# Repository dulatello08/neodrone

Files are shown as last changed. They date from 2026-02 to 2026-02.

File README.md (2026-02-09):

# NeoDrone v1

NeoDrone v1 is a compact all-in-one flight controller + 4-in-1 ESC board for small custom drones.

## Why I made this project

I wanted a cleaner drone stack with fewer separate boards, less wiring, and tighter integration between control and motor drive.  
This project is also a learning build to improve my PCB, embedded, and drone-systems workflow end to end.

## How to use this project

1. Clone this repository.
2. Pull firmware submodule:
   ```bash
   git submodule update --init --recursive
   ```
3. Open the hardware design in KiCad from `hardware/design/neodrone-v1.kicad_pro`.
4. Use firmware from `firmware/` (submodule) or project write-up links below.

Project links:

- [NeoDrone 3D model notes](https://dulatello08.me/blog/neodrone-3d-model/)
- [NeoDrone firmware notes](https://dulatello08.me/blog/neodrone-firmware/)
- [NeoDrone progress log #1](https://dulatello08.me/blog/neodrone-progress-1/)

### Full 3D model screenshot

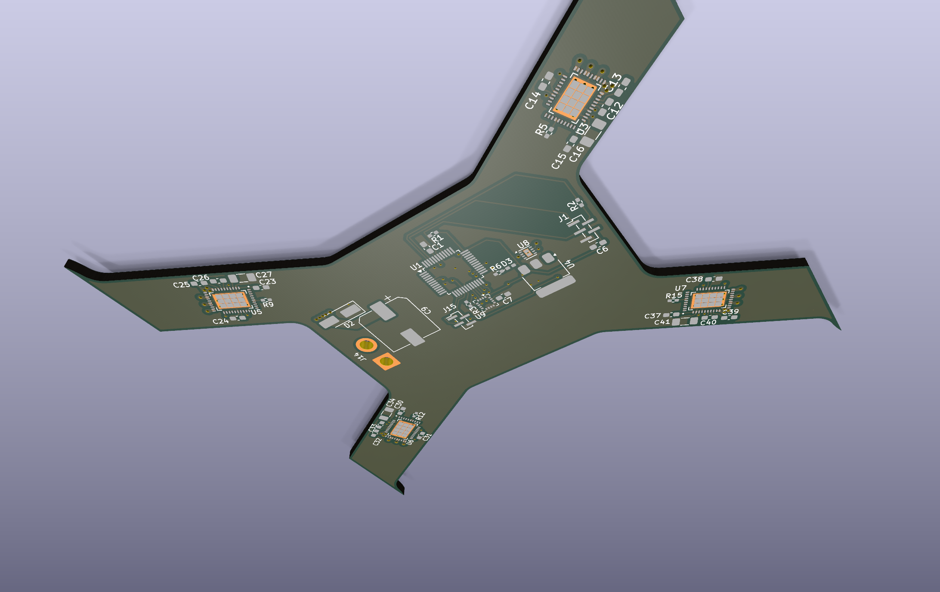
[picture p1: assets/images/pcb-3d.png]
NeoDrone v1 full 3D model


### PCB screenshot

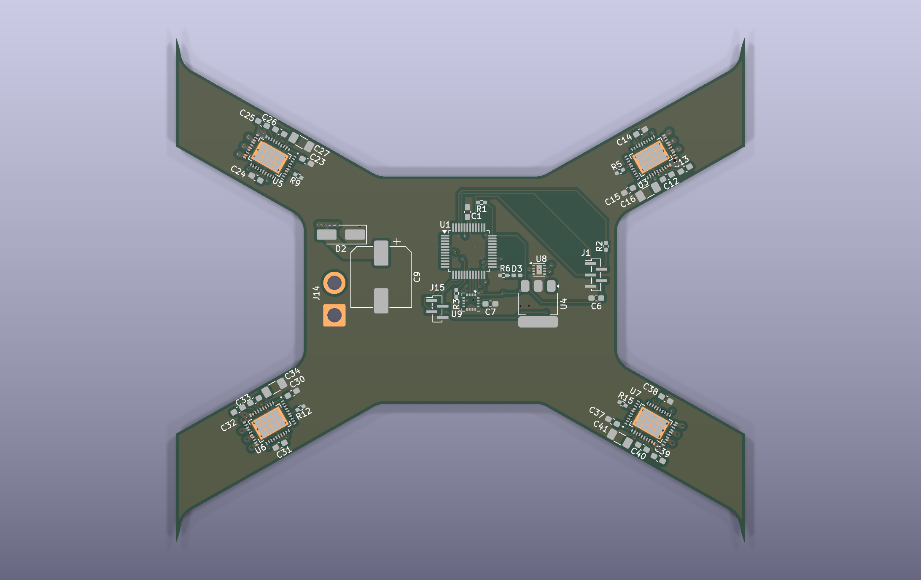
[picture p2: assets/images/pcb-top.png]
NeoDrone v1 PCB screenshot


### Wiring diagram

External wiring used: 4 motors (M1-M4), battery (VBAT/GND), and CRSF receiver (UART + power).

```mermaid
flowchart LR
  Battery["Battery"] --> FC["NeoDrone v1 Board"]
  FC --> M1["Motor 1"]
  FC --> M2["Motor 2"]
  FC --> M3["Motor 3"]
  FC --> M4["Motor 4"]
  CRSF["CRSF Receiver"] --> FC
```

## BOM (truncated)

Full BOM export is in `bom.csv`.  
This is a shortened reference table with links:

| Reference | Part | MPN | Qty | Link |
|---|---|---|---:|---|
| U1 | Main MCU | ATSAMD21G18A-AU | 1 | [Digi-Key](https://www.digikey.com/en/products/result?keywords=ATSAMD21G18A-AU-ND) |
| U3, U5, U6, U7 | 3-phase motor driver | MCF8316A1VRGFR | 4 | [Digi-Key](https://www.digikey.com/en/products/result?keywords=296-MCF8316A1VRGFRCT-ND) |
| U4 | 3.3V regulator | MCP1826S-3302E/DB | 1 | [Digi-Key](https://www.digikey.com/en/products/result?keywords=MCP1826S-3302E%2FDB-ND) |
| U8 | 5V buck regulator | TPS62163DSGT | 1 | [Digi-Key](https://www.digikey.com/en/products/result?keywords=296-30228-1-ND) |
| U9 | IMU | ICM-20602 | 1 | [Digi-Key](https://www.digikey.com/en/products/result?keywords=1428-1060-1-ND) |
| Q1 | P-channel MOSFET | SI7139DP-T1-GE3 | 1 | [Digi-Key](https://www.digikey.com/en/products/result?keywords=SI7139DP-T1-GE3CT-ND) |
| L1-L5 | 2.2uH inductors | SRN2510BTA-2R2M | 5 | [Digi-Key](https://www.digikey.com/en/products/result?keywords=118-SRN2510BTA-2R2MCT-ND) |
| D1 | 12V zener diode | BZT52B12 RHG | 1 | [Digi-Key](https://www.digikey.com/en/products/result?keywords=BZT52B12RHGCT-ND) |
| D2 | TVS diode | SMAJ18A-13-F | 1 | [Digi-Key](https://www.digikey.com/en/products/result?keywords=SMAJ18A-FDICT-ND) |
| C9 | Bulk electrolytic cap | EEE-FP1E331AP | 1 | [Digi-Key](https://www.digikey.com/en/products/result?keywords=PCE4439CT-ND) |

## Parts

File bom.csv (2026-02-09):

Index | Manufacturer Part Number | Manufacturer Name | Description | Lead Time | Availability | Stock Status | Attrition % | Requested Quantity 1 | Pack Quantity 1 | Pack Type 1 | Digi-Key Part Number 1 | Unit Price 1 | Extended Price 1 | Minimum Order Quantity 1 | Customer Reference | Requested Part Number | Lead Weeks | Datasheet | Reference Designator | US Import Tariff | Note | Part Status | RoHS Status | REACH Status | Moisture Sensitivity Level (MSL) | ECCN | HTSUS | Country of Origin | Environmental Information | Original Part numbers | Unit of Measure | Image | Product Notes
1 | GCM188R71C105KA64D | Murata Electronics | CAP CER 1UF 16V X7R 0603 |  | 600,773 | In Stock | 10 | 13 | 15 | Cut Tape (CT) | 490-5241-1-ND | 0.08500 | $1.28 | 1 |  | 490-5241-1-ND | 16 | https://pim.murata.com/asset/pim4/ceramicCapacitorSMD/GCM188R71C105KA64-04A-EN_PDF_CERAMICCAPACITORSMD |  | - |  | Active | ROHS3 Compliant | REACH Unaffected | 1 (Unlimited) | EAR99 | 8532.24.0020 | Philippines |  | 490-5241-1-ND | EACH | https://mm.digikey.com/Volume0/opasdata/d220001/medias/images/4850/490_0603%20%281608%20metric%29.jpg
2 | CC1206KKX5R8BB226 | YAGEO | CAP CER 22UF 25V X5R 1206 |  | 1,675 | In Stock | 10 | 10 | 11 | Cut Tape (CT) | 13-CC1206KKX5R8BB226CT-ND | 0.38600 | $4.25 | 1 |  | 13-CC1206KKX5R8BB226CT-ND | 24 | https://yageogroup.com/content/datasheet/asset/file/UPY-GPHC_X5R_4V-TO-50V |  | - |  | Active | ROHS3 Compliant | REACH Unaffected | 1 (Unlimited) | EAR99 | 8532.24.0020 | Taiwan |  | 1276-3047-1-ND | EACH | https://mm.digikey.com/Volume0/opasdata/d220001/medias/images/4848/13_1206-%283216-Metric%29-1%2C45mm.jpg
3 | GRM188R72A104KA35D | Murata Electronics | CAP CER 0.1UF 100V X7R 0603 |  | 1,699,041 | In Stock | 10 | 12 | 14 | Cut Tape (CT) | 490-3285-1-ND | 0.08700 | $1.22 | 1 |  | 490-3285-1-ND | 12 | https://search.murata.co.jp/Ceramy/image/img/A01X/G101/ENG/GRM188R72A104KA35-01.pdf |  | - |  | Active | ROHS3 Compliant | REACH Unaffected | 1 (Unlimited) | EAR99 | 8532.24.0020 | Japan |  | 490-3285-1-ND | EACH | https://mm.digikey.com/Volume0/opasdata/d220001/medias/images/4322/cut-tape-render.jpg
4 | CGJ3E2X7R1H473K080AA | TDK Corporation | CAP CER 0.047UF 50V X7R 0603 |  | 9,349 | In Stock - Non-Stock | 10 | 4 | 5 | Cut Tape (CT) | 445-8120-1-ND | 0.17000 | $0.85 | 1 |  | 445-8120-1-ND | 36 | https://product.tdk.com/en/system/files/dam/doc/product/capacitor/ceramic/mlcc/catalog/mlcc_highreliability_general_en.pdf |  | - |  | Obsolete | ROHS3 Compliant | REACH Unaffected | 1 (Unlimited) | EAR99 | 8532.24.0020 | Japan | https://product.tdk.com/system/files/dam/doc/product/capacitor/ceramic/mlcc/rohs/mlccrohs_highreliability_general_en.pdf|https://product.tdk.com/en/environment/index.html | 445-8120-1-ND | EACH | https://mm.digikey.com/Volume0/opasdata/d220001/medias/images/2640/MFG_CGJ3E2X7R1H473K080AA.jpg
5 | CL10A106MA8NRNC | Samsung Electro-Mechanics | CAP CER 10UF 25V X5R 0603 |  | 655,915 | In Stock | 10 | 3 | 4 | Cut Tape (CT) | 1276-1869-1-ND | 0.09000 | $0.36 | 1 |  | 1276-1869-1-ND | 31 | https://mm.digikey.com/Volume0/opasdata/d220001/medias/docus/658/CL10A106MA8NRNC_Spec.pdf |  | - |  | Active | ROHS3 Compliant | REACH Unaffected | 1 (Unlimited) | EAR99 | 8532.24.0020 | China | https://www.samsungsem.com/files/fileDown.do?key=ed1dfdfa-645e-4252-b707-17f9b1502dd1|https://www.samsungsem.com/global/support/certificate/product-stewardship.do | 1276-1869-1-ND | EACH | https://mm.digikey.com/Volume0/opasdata/d220001/medias/images/2537/Ceramic-Capacitor-CL-Series.jpg
6 | CC0402KRX7R9BB103 | YAGEO | CAP CER 10000PF 50V X7R 0402 |  | 2,772,907 | In Stock | 10 | 1 | 2 | Cut Tape (CT) | 311-1349-1-ND | 0.08000 | $0.16 | 1 |  | 311-1349-1-ND | 16 | https://yageogroup.com/content/datasheet/asset/file/UPY-GPHC_X7R_6_3V-TO-250V |  | - |  | Active | ROHS3 Compliant | REACH Unaffected | 1 (Unlimited) | EAR99 | 8532.24.0020 | Taiwan |  | 311-1349-1-ND | EACH | https://mm.digikey.com/Volume0/opasdata/d220001/medias/images/4322/cut-tape-render.jpg
7 | GRM188R61H225KE11D | Murata Electronics | CAP CER 2.2UF 50V X5R 0603 |  | 74,531 | In Stock | 10 | 1 | 2 | Cut Tape (CT) | 490-10733-1-ND | 0.25000 | $0.50 | 1 |  | 490-10733-1-ND | 12 | https://search.murata.co.jp/Ceramy/image/img/A01X/G101/ENG/GRM188R61H225KE11-01.pdf |  | - |  | Active | ROHS3 Compliant | REACH Unaffected | 1 (Unlimited) | EAR99 | 8532.24.0020 | Japan |  | 490-10733-1-ND | EACH | https://mm.digikey.com/Volume0/opasdata/d220001/medias/images/4322/cut-tape-render.jpg
8 | GRM188R61E475KE11D | Murata Electronics | CAP CER 4.7UF 25V X5R 0603 |  | 286,809 | In Stock | 10 | 1 | 2 | Cut Tape (CT) | 490-7203-1-ND | 0.08000 | $0.16 | 1 |  | 490-7203-1-ND | 12 | https://search.murata.co.jp/Ceramy/image/img/A01X/G101/ENG/GRM188R61E475KE11-01.pdf |  | - |  | Active | ROHS3 Compliant | REACH Unaffected | 1 (Unlimited) | EAR99 | 8532.24.0020 | Japan |  | 490-7203-1-ND | EACH | https://mm.digikey.com/Volume0/opasdata/d220001/medias/images/4322/cut-tape-render.jpg
9 | EEE-FP1E331AP | Panasonic Electronic Components | CAP ALUM 330UF 20% 25V SMD |  | 14,767 | In Stock | 10 | 1 | 2 | Cut Tape (CT) | PCE4439CT-ND | 1.00000 | $2.00 | 1 |  | PCE4439CT-ND | 18 | https://industrial.panasonic.com/ww/products/pt/aluminum-cap-smd/models/EEEFP1E331AP |  | - |  | Active | ROHS3 Compliant | REACH Unaffected | 1 (Unlimited) | EAR99 | 8532.22.0020 | Malaysia |  | PCE4439CT-ND | EACH | https://mm.digikey.com/Volume0/opasdata/d220001/medias/images/634/EEE-FP1V221AP.JPG
10 | BZT52B12 RHG | Taiwan Semiconductor Corporation | DIODE ZENER 12V 500MW SOD123F |  | 7,787 | In Stock | 10 | 1 | 2 | Cut Tape (CT) | BZT52B12RHGCT-ND | 0.15000 | $0.30 | 1 |  | BZT52B12RHGCT-ND | 18 | https://services.taiwansemi.com/storage/resources/datasheet/BZT52B2V4 series_F15.pdf |  | - |  | Active | ROHS3 Compliant | REACH Unaffected | 1 (Unlimited) | EAR99 | 8541.10.0050 | Taiwan | https://www.taiwansemi.com/en/wp-content/uploads/2023/12/Environment_Hazardous_Substances_Compliance_20231115.pdf|https://www.taiwansemi.com/en/wp-content/uploads/2023/12/REACH_regulation1907_2006_EC_compliance_240%20SVHCs_20240124_Web.pdf|https://services.taiwansemi.com/storage/resources/environmental_information/REACH%20regulation%20compliance_ANNEX%20XVII_20250708_Web.pdf|https://www.taiwansemi.com/en/wp-content/uploads/2023/12/California%20Proposition%2065%20Compliance_20240124_Web.pdf | 1727-1597-1-ND | EACH | https://mm.digikey.com/Volume0/opasdata/d220001/medias/images/6241/1801%7ESOD123F%7E%7E2_view2.jpg
11 | SMAJ18A-13-F | Diodes Incorporated | TVS DIODE 18VWM 29.2VC SMA |  | 113,230 | In Stock | 10 | 1 | 2 | Cut Tape (CT) | SMAJ18A-FDICT-ND | 0.20000 | $0.40 | 1 |  | SMAJ18A-FDICT-ND | 12 | https://www.diodes.com/assets/Datasheets/SMAJ5.0CA-SMAJ200CA.pdf |  | - |  | Active | ROHS3 Compliant | REACH Unaffected | 1 (Unlimited) | EAR99 | 8541.10.0080 | Taiwan | https://mm.digikey.com/Volume0/opasdata/d220001/medias/docus/6731/Diode%20RoHS3%20REACH%20247%20Jan%202025%20Statement.pdf | 1655-SMAJ18ACT-ND | EACH | https://mm.digikey.com/Volume0/opasdata/d220001/medias/images/5787/31%7ESMA%7E%7E2-View-2.jpg
12 | LTST-C281KRKT | Lite-On Inc. | LED RED CLEAR CHIP SMD |  | 21,252 | In Stock | 10 | 1 | 2 | Cut Tape (CT) | 160-LTST-C281KRKTCT-ND | 0.18000 | $0.36 | 1 |  | 160-LTST-C281KRKTCT-ND | 22 | https://optoelectronics.liteon.com/upload/download/DS22-2008-0117/LTST-C281KRKT.pdf |  | May apply on shipments to the U.S. |  | Active | ROHS3 Compliant | REACH Unaffected | 2A (4 Weeks) | EAR99 | 8541.41.0000 | China |  | 160-LTST-C281KRKTCT-ND | EACH | https://mm.digikey.com/Volume0/opasdata/d220001/derivates/6/003/237/303/%7E160%7E0402-%281005-Metric%29%7E.002_web%28640x640%29.jpg
13 | BC070-05-A-1-L-C | GCT | 5POS 1.0MM PITCH SOCKET, SIL, SM |  | 2,899 | In Stock |  | 1 | 1 | Cut Tape (CT) | 2073-BC070-05-A-1-L-CCT-ND | 1.03000 | $1.03 | 1 |  | 2073-BC070-05-A-1-L-CCT-ND | 8 | https://gct.co/files/specs/1.00mm-socket-spec.pdf |  | May apply on shipments to the U.S. |  | Active | ROHS3 Compliant | REACH Unaffected | 1 (Unlimited) | EAR99 | 8536.69.4040 | China | https://gct.co/files/info/gct_certificate_of_compliance.pdf | 2073-BC070-05-A-1-L-CCT-ND | EACH | https://mm.digikey.com/Volume0/opasdata/d220001/medias/images/438/MFG_BC070-05-A-1-L-C.jpg
14 | BC070-04-A-1-L-D | GCT | 4W, 1.0MM PITCH SOCKET, SIL, SMT |  | 2,866 | In Stock |  | 1 | 1 | Tube | 2073-BC070-04-A-1-L-D-ND | 0.52000 | $0.52 | 1 |  | 2073-BC070-04-A-1-L-D-ND | 8 | https://gct.co/files/specs/1.00mm-socket-spec.pdf |  | May apply on shipments to the U.S. |  | Active | ROHS3 Compliant | REACH Unaffected | 1 (Unlimited) | EAR99 | 8536.69.4040 | China | https://gct.co/files/info/gct_certificate_of_compliance.pdf | 2073-BC070-04-A-1-L-D-ND | EACH | https://mm.digikey.com/Volume0/opasdata/d220001/medias/images/4059/BC070-04-A-1-L-D.jpg
15 | SRN2510BTA-2R2M | Bourns Inc. | FIXED IND 2.2UH 2A 132 MOHM SMD |  | 2,140 | In Stock | 10 | 5 | 6 | Cut Tape (CT) | 118-SRN2510BTA-2R2MCT-ND | 0.30000 | $1.80 | 1 |  | 118-SRN2510BTA-2R2MCT-ND | 21 | https://www.bourns.com/docs/Product-Datasheets/SRN2510BTA.pdf |  | May apply on shipments to the U.S. |  | Active | ROHS3 Compliant | REACH Unaffected | 1 (Unlimited) | EAR99 | 8504.50.8000 | China | https://mm.digikey.com/Volume0/opasdata/d220001/medias/docus/6657/Bourns%20REACH%20247%20Jan%202025%20Statement.pdf|https://www.bourns.com/docs/rohs-cofc/cofc-srn.pdf?sfvrsn=597d93f1_18 | 118-SRN2510BTA-2R2MCT-ND | EACH | https://mm.digikey.com/Volume0/opasdata/d220001/derivates/6/001/152/398/MFG_SRN2510BTA_web%28640x640%29.jpg
16 | SI7139DP-T1-GE3 | Vishay Siliconix | MOSFET P-CH 30V 40A PPAK SO-8 |  | 4,126 | In Stock |  | 1 | 1 | Cut Tape (CT) | SI7139DP-T1-GE3CT-ND | 2.09000 | $2.09 | 1 |  | SI7139DP-T1-GE3CT-ND | 39 | https://www.vishay.com/docs/65299/si7139dp.pdf |  | May apply on shipments to the U.S. |  | Active | ROHS3 Compliant |  | 1 (Unlimited) | EAR99 | 8541.29.0095 | China |  | SI7139DP-T1-GE3CT-ND | EACH | https://mm.digikey.com/Volume0/opasdata/d220001/derivates/6/003/212/993/742%7E5881%7EDP%7E8_web%28640x640%29.jpg
17 | RC0402FR-0710KL | YAGEO | RES 10K OHM 1% 1/16W 0402 |  | 9,636,776 | In Stock | 10 | 10 | 11 | Cut Tape (CT) | 311-10.0KLRCT-ND | 0.01200 | $0.13 | 1 |  | 311-10.0KLRCT-ND | 18 | https://yageogroup.com/content/datasheet/asset/file/PYU-RC_GROUP_51_ROHS_L |  | - |  | Active | ROHS3 Compliant | REACH Unaffected | 1 (Unlimited) | EAR99 | 8533.21.0030 | Taiwan | https://www.yageogroup.com/content/Resource%20Library/Product%20Environmental%20Compliance/RoHS_Compliance_YAGEO.pdf | 311-10.0KLRCT-ND | EACH | https://mm.digikey.com/Volume0/opasdata/d220001/medias/images/4322/cut-tape-render.jpg
18 | RC0402FR-07100KL | YAGEO | RES 100K OHM 1% 1/16W 0402 |  | 4,831,519 | In Stock | 10 | 1 | 2 | Cut Tape (CT) | 311-100KLRCT-ND | 0.10000 | $0.20 | 1 |  | 311-100KLRCT-ND | 18 | https://yageogroup.com/content/datasheet/asset/file/PYU-RC_GROUP_51_ROHS_L |  | - |  | Active | ROHS3 Compliant | REACH Unaffected | 1 (Unlimited) | EAR99 | 8533.21.0030 | Taiwan | https://www.yageogroup.com/content/Resource%20Library/Product%20Environmental%20Compliance/RoHS_Compliance_YAGEO.pdf | 311-100KLRCT-ND | EACH | https://mm.digikey.com/Volume0/opasdata/d220001/medias/images/4322/cut-tape-render.jpg
19 | RC0402FR-0733RL | YAGEO | RES 33 OHM 1% 1/16W 0402 |  | 2,592,460 | In Stock | 10 | 1 | 2 | Cut Tape (CT) | 311-33.0LRCT-ND | 0.10000 | $0.20 | 1 |  | 311-33.0LRCT-ND | 18 | https://yageogroup.com/content/datasheet/asset/file/PYU-RC_GROUP_51_ROHS_L |  | - |  | Active | ROHS3 Compliant | REACH Unaffected | 1 (Unlimited) | EAR99 | 8533.21.0030 | Taiwan | https://www.yageogroup.com/content/Resource%20Library/Product%20Environmental%20Compliance/RoHS_Compliance_YAGEO.pdf | 311-33.0LRCT-ND | EACH | https://mm.digikey.com/Volume0/opasdata/d220001/medias/images/4322/cut-tape-render.jpg
20 | RC0402FR-07220RL | YAGEO | RES 220 OHM 1% 1/16W 0402 |  | 410,791 | In Stock | 10 | 1 | 2 | Cut Tape (CT) | 311-220LRCT-ND | 0.10000 | $0.20 | 1 |  | 311-220LRCT-ND | 18 | https://yageogroup.com/content/datasheet/asset/file/PYU-RC_GROUP_51_ROHS_L |  | - |  | Active | ROHS3 Compliant | REACH Unaffected | 1 (Unlimited) | EAR99 | 8533.21.0030 | Taiwan | https://www.yageogroup.com/content/Resource%20Library/Product%20Environmental%20Compliance/RoHS_Compliance_YAGEO.pdf | 311-220LRCT-ND | EACH | https://mm.digikey.com/Volume0/opasdata/d220001/medias/images/4322/cut-tape-render.jpg
21 | ATSAMD21G18A-AU | Microchip Technology | IC MCU 32BIT 256KB FLASH 48TQFP |  | 6,577 | In Stock |  | 1 | 1 | Tray | ATSAMD21G18A-AU-ND | 4.16000 | $4.16 | 1 |  | ATSAMD21G18A-AU-ND | 4 | https://ww1.microchip.com/downloads/en/DeviceDoc/SAM-D21-DA1-Family-Data-Sheet-DS40001882H.pdf |  | - |  | Active | ROHS3 Compliant | REACH Unaffected | 3 (168 Hours) | 3A991A2 | 8542.31.0025 | Thailand | https://ww1.microchip.com/downloads/aemDocuments/documents/corporate-responsibilty/environmental/product-regulatory-information/Semiconductor_EnvCoC.pdf|https://ww1.microchip.com/downloads/aemDocuments/documents/corporate-responsibilty/environmental/product-regulatory-information/Microchip_REACH_Statement.pdf | ATSAMD21G18A-AU-ND | EACH | https://mm.digikey.com/Volume0/opasdata/d220001/medias/images/4578/150%7E48TQFP-1%2C2-7x7%7EA%7E48.JPG
22 | MCF8316A1VRGFR | Texas Instruments | 40-V MAX, 8-A PEAK, SENSORLESS F |  | 3,958 | In Stock |  | 4 | 4 | Cut Tape (CT) | 296-MCF8316A1VRGFRCT-ND | 3.91000 | $15.64 | 1 |  | 296-MCF8316A1VRGFRCT-ND | 12 | https://www.ti.com/lit/ds/symlink/mcf8316a.pdf?ts=1662971630101 |  | - |  | Active | Not applicable |  | 2 (1 Year) | EAR99 | 8542.39.0070 | China |  | 296-MCF8316A1VRGFRCT-ND | EACH | https://mm.digikey.com/Volume0/opasdata/d220001/derivates/6/003/210/417/296%7E4204716-3%7ERGF%7E40_web%28640x640%29.jpg
23 | MCP1826S-3302E/DB | Microchip Technology | IC REG LINEAR 3.3V 1A SOT-223-3 |  | 9,244 | In Stock |  | 1 | 1 | Tube | MCP1826S-3302E/DB-ND | 0.91000 | $0.91 | 1 |  | MCP1826S-3302E/DB-ND | 4 | https://ww1.microchip.com/downloads/en/DeviceDoc/22057B.pdf |  | - |  | Active | ROHS3 Compliant | REACH Unaffected | 1 (Unlimited) | EAR99 | 8542.39.0090 | Thailand | https://ww1.microchip.com/downloads/aemDocuments/documents/corporate-responsibilty/environmental/product-regulatory-information/Semiconductor_EnvCoC.pdf|https://ww1.microchip.com/downloads/aemDocuments/documents/corporate-responsibilty/environmental/product-regulatory-information/Microchip_REACH_Statement.pdf | MCP1826S-3302E/DB-ND | EACH | https://mm.digikey.com/Volume0/opasdata/d220001/medias/images/5484/150%7EC04-032%7EDB%7E4.JPG
24 | TPS62163DSGT | Texas Instruments | IC REG BUCK 5V 1A 8WSON |  | 8,333 | In Stock |  | 1 | 1 | Cut Tape (CT) | 296-30228-1-ND | 1.98000 | $1.98 | 1 |  | 296-30228-1-ND | 12 | https://www.ti.com/general/docs/suppproductinfo.tsp?distId=10 |  | - |  | Active | ROHS3 Compliant | REACH Unaffected | 2 (1 Year) | EAR99 | 8542.39.0090 | Malaysia |  | 296-30228-1-ND | EACH | https://mm.digikey.com/Volume0/opasdata/d220001/medias/images/339/296%7E4208210%7EDSG%7E8.jpg
25 | ICM-20602 | TDK InvenSense | IMU ACCEL/GYRO/TEMP I2C/SPI LGA |  | 75 | In Stock |  | 1 | 1 | Cut Tape (CT) | 1428-1060-1-ND | 4.96000 | $4.96 | 1 |  | 1428-1060-1-ND | 26 | https://www.invensense.com/wp-content/uploads/2016/10/DS-000176-ICM-20602-v1.0.pdf |  | - |  | Last Time Buy | ROHS3 Compliant | REACH Unaffected | 3 (168 Hours) | 7A994 | 8542.39.0070 | Taiwan |  | 1428-1060-1-ND | EACH | https://mm.digikey.com/Volume0/opasdata/d220001/medias/images/6154/1428%7E16LGA-.80-3X3%7E%7E16.jpg

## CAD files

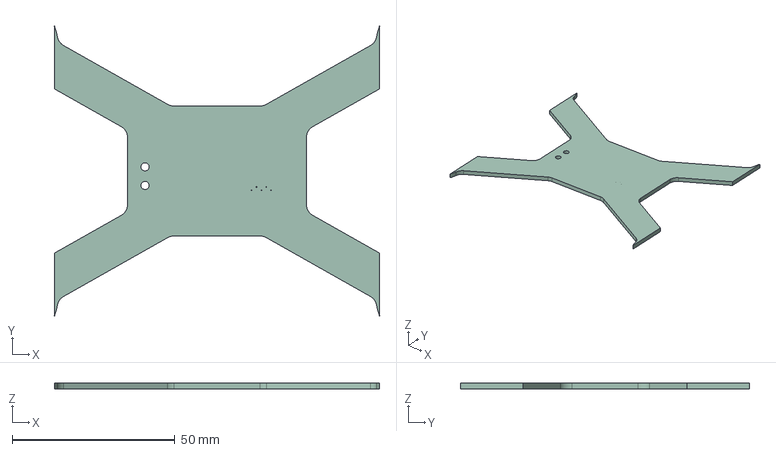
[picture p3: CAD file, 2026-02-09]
hardware/3d/neodrone-v1.step
100.0 x 89.0 x 1.84 mm

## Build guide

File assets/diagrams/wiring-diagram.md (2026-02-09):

# NeoDrone v1 wiring diagram

Current planned wiring:

- 4 motors connected directly to board outputs M1-M4
- battery connected to VBAT and GND
- CRSF receiver connected to power and UART (TX/RX + GND)

```mermaid
flowchart LR
  Battery["Battery"] --> FC["NeoDrone v1 Board"]
  FC --> M1["Motor 1"]
  FC --> M2["Motor 2"]
  FC --> M3["Motor 3"]
  FC --> M4["Motor 4"]
  CRSF["CRSF Receiver"] --> FC
```

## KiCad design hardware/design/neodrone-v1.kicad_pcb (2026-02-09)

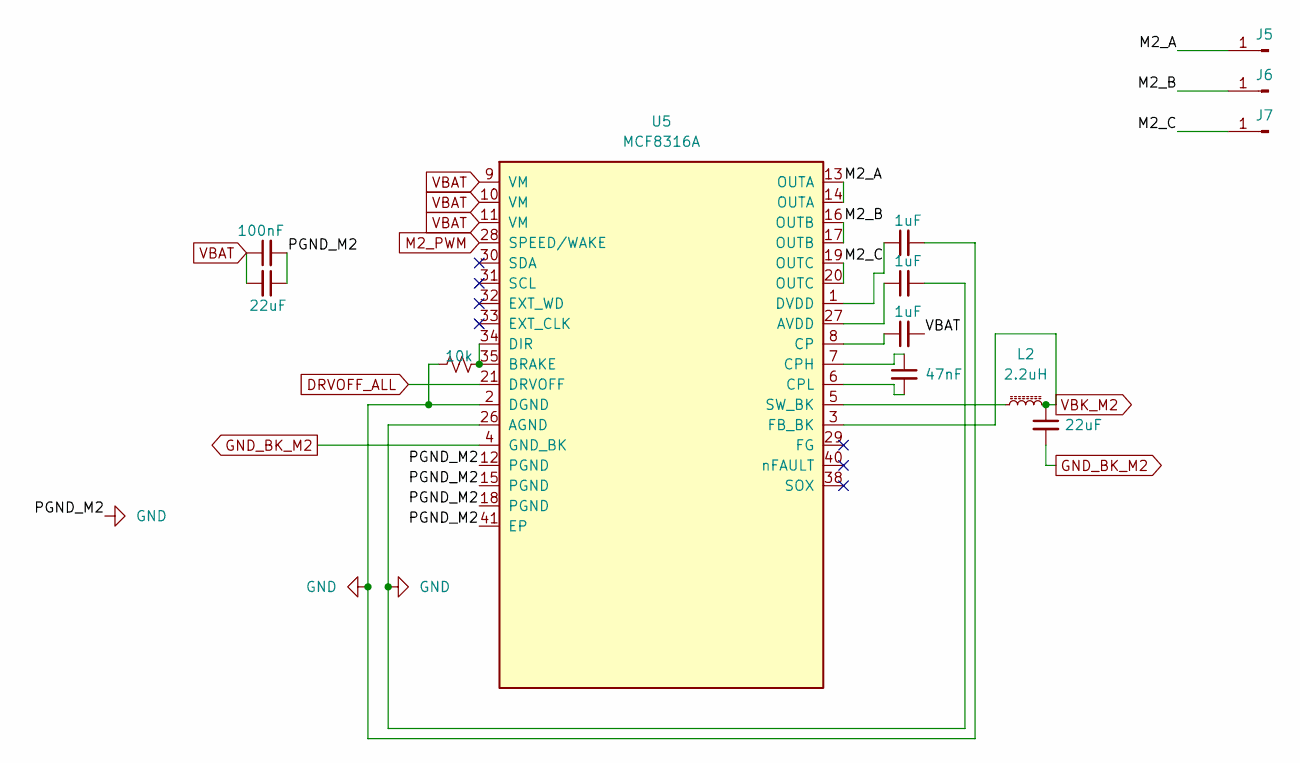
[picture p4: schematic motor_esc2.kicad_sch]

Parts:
C21: 100nF; C_0603_1608Metric_Pad1.08x0.95mm_HandSolder
C22, C27: 22uF; C_1206_3216Metric_Pad1.33x1.80mm_HandSolder
C23, C24, C25: 1uF; C_0603_1608Metric_Pad1.08x0.95mm_HandSolder
C26: 47nF; C_0603_1608Metric_Pad1.08x0.95mm_HandSolder
J5, J6, J7: SolderWirePad_1x01_SMD_2x4mm
L2: 2.2uH; L_1008_2520Metric_Pad1.43x2.20mm_HandSolder
R9: 10k; R_0402_1005Metric_Pad0.72x0.64mm_HandSolder
U5: MCF8316A; MCF8316A_RGF0040E_VQFN-40-1EP_7x5mm_P0.5mm_EP5.5x3.5mm

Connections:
/motor_esc2/M2_A: J5.1, U5.13 (OUTA), U5.14 (OUTA)
/motor_esc2/M2_B: J6.1, U5.16 (OUTB), U5.17 (OUTB)
/motor_esc2/M2_C: J7.1, U5.19 (OUTC), U5.20 (OUTC)
DRVOFF_ALL: U5.21 (DRVOFF); also elsewhere on the board
GND: C21.2, C22.1, C23.2, C24.2, C27.2, R9.1, U5.2 (DGND), U5.4 (GND_BK), U5.12 (PGND), U5.15 (PGND), U5.18 (PGND), U5.26 (AGND), U5.41 (EP); also elsewhere on the board
M2_PWM: U5.28 (SPEED/WAKE); also elsewhere on the board
unnamed: C24.1, U5.27 (AVDD)
unnamed: R9.2, U5.34 (DIR), U5.35 (BRAKE)
unnamed: C25.1, U5.8 (CP)
unnamed: C26.1, U5.7 (CPH)
unnamed: C26.2, U5.6 (CPL)
unnamed: C23.1, U5.1 (DVDD)
unnamed: L2.1, U5.5 (SW_BK)
VBAT: C21.1, C22.2, C25.2, U5.9 (VM), U5.10 (VM), U5.11 (VM); also elsewhere on the board
VBK_M2: C27.1, L2.2, U5.3 (FB_BK)

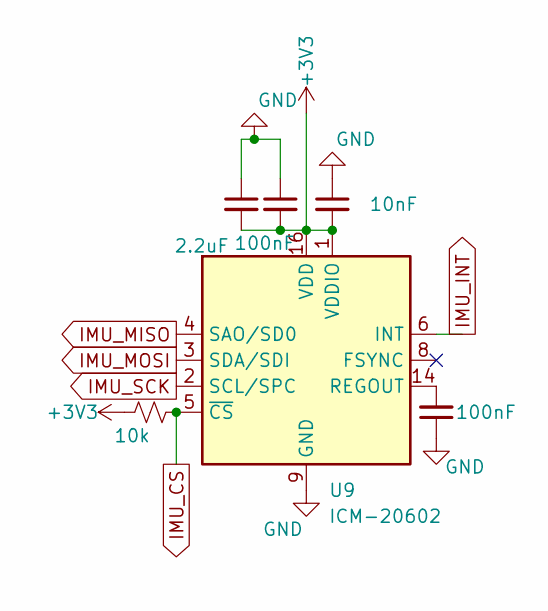
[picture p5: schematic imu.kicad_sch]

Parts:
C7, C8: 100nF; C_0603_1608Metric_Pad1.08x0.95mm_HandSolder
C44: 10nF; C_0402_1005Metric_Pad0.74x0.62mm_HandSolder
C45: 2.2uF; C_0603_1608Metric_Pad1.08x0.95mm_HandSolder
R3: 10k; R_0402_1005Metric_Pad0.72x0.64mm_HandSolder
U9: ICM-20602; LGA-16_3x3mm_P0.5mm

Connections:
+3V3: C8.2, C44.2, C45.2, R3.1, U9.1 (VDDIO), U9.16 (VDD); also elsewhere on the board
GND: C7.1, C8.1, C44.1, C45.1, U9.9 (GND), U9.10 (GND), U9.11 (GND), U9.12 (GND), U9.13 (GND), U9.15 (GND); also elsewhere on the board
IMU_CS: R3.2, U9.5 (~CS); also elsewhere on the board
IMU_INT: U9.6 (INT); also elsewhere on the board
IMU_MISO: U9.4 (SAO/SD0); also elsewhere on the board
IMU_MOSI: U9.3 (SDA/SDI); also elsewhere on the board
IMU_SCK: U9.2 (SCL/SPC); also elsewhere on the board
unnamed: C7.2, U9.14 (REGOUT)

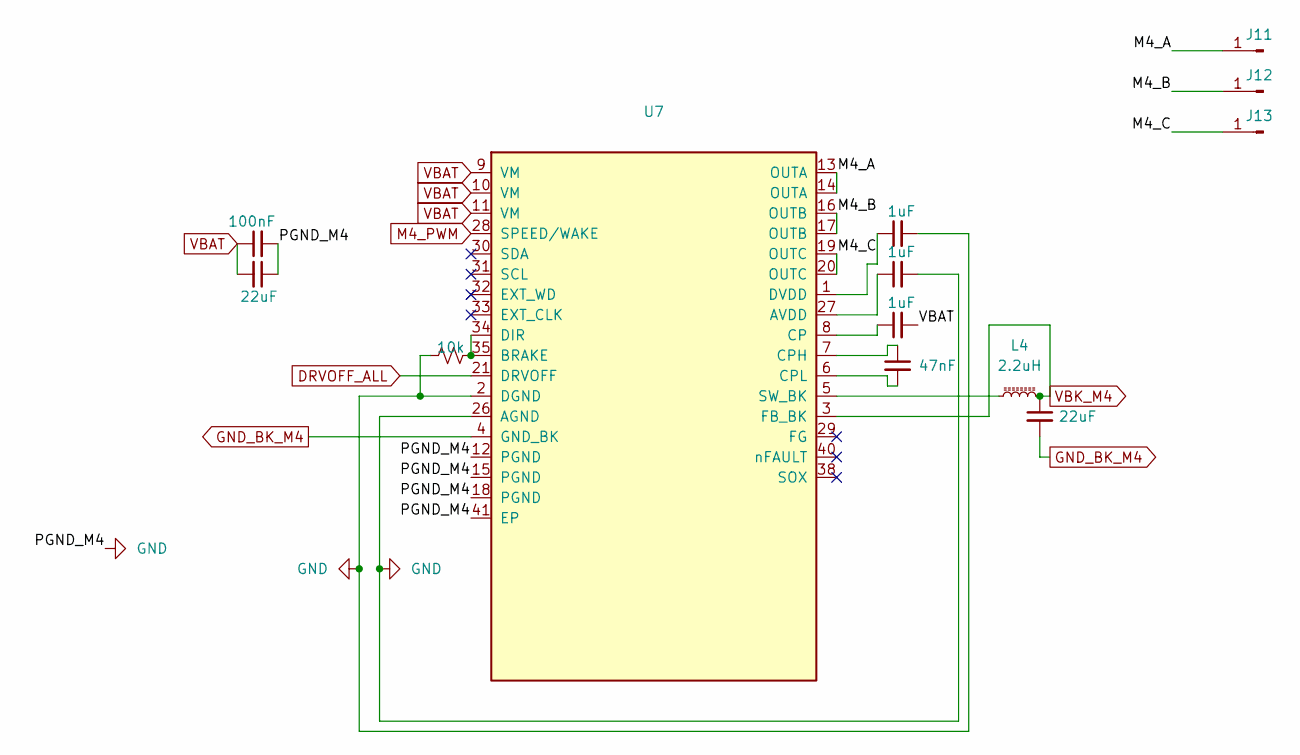
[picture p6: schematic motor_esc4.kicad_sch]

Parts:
C35: 100nF; C_0603_1608Metric_Pad1.08x0.95mm_HandSolder
C36, C41: 22uF; C_1206_3216Metric_Pad1.33x1.80mm_HandSolder
C37, C38, C39: 1uF; C_0603_1608Metric_Pad1.08x0.95mm_HandSolder
C40: 47nF; C_0603_1608Metric_Pad1.08x0.95mm_HandSolder
J11, J12, J13: SolderWirePad_1x01_SMD_2x4mm
L4: 2.2uH; L_1008_2520Metric_Pad1.43x2.20mm_HandSolder
R15: 10k; R_0402_1005Metric_Pad0.72x0.64mm_HandSolder
U7: MCF8316A; MCF8316A_RGF0040E_VQFN-40-1EP_7x5mm_P0.5mm_EP5.5x3.5mm

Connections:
/motor_esc4/M4_A: J11.1, U7.13 (OUTA), U7.14 (OUTA)
/motor_esc4/M4_B: J12.1, U7.16 (OUTB), U7.17 (OUTB)
/motor_esc4/M4_C: J13.1, U7.19 (OUTC), U7.20 (OUTC)
DRVOFF_ALL: U7.21 (DRVOFF); also elsewhere on the board
GND: C35.2, C36.1, C37.2, C38.2, C41.2, R15.1, U7.2 (DGND), U7.4 (GND_BK), U7.12 (PGND), U7.15 (PGND), U7.18 (PGND), U7.26 (AGND), U7.41 (EP); also elsewhere on the board
M4_PWM: U7.28 (SPEED/WAKE); also elsewhere on the board
unnamed: C38.1, U7.27 (AVDD)
unnamed: R15.2, U7.34 (DIR), U7.35 (BRAKE)
unnamed: C39.1, U7.8 (CP)
unnamed: C40.1, U7.7 (CPH)
unnamed: C40.2, U7.6 (CPL)
unnamed: C37.1, U7.1 (DVDD)
unnamed: L4.1, U7.5 (SW_BK)
VBAT: C35.1, C36.2, C39.2, U7.9 (VM), U7.10 (VM), U7.11 (VM); also elsewhere on the board
VBK_M4: C41.1, L4.2, U7.3 (FB_BK)

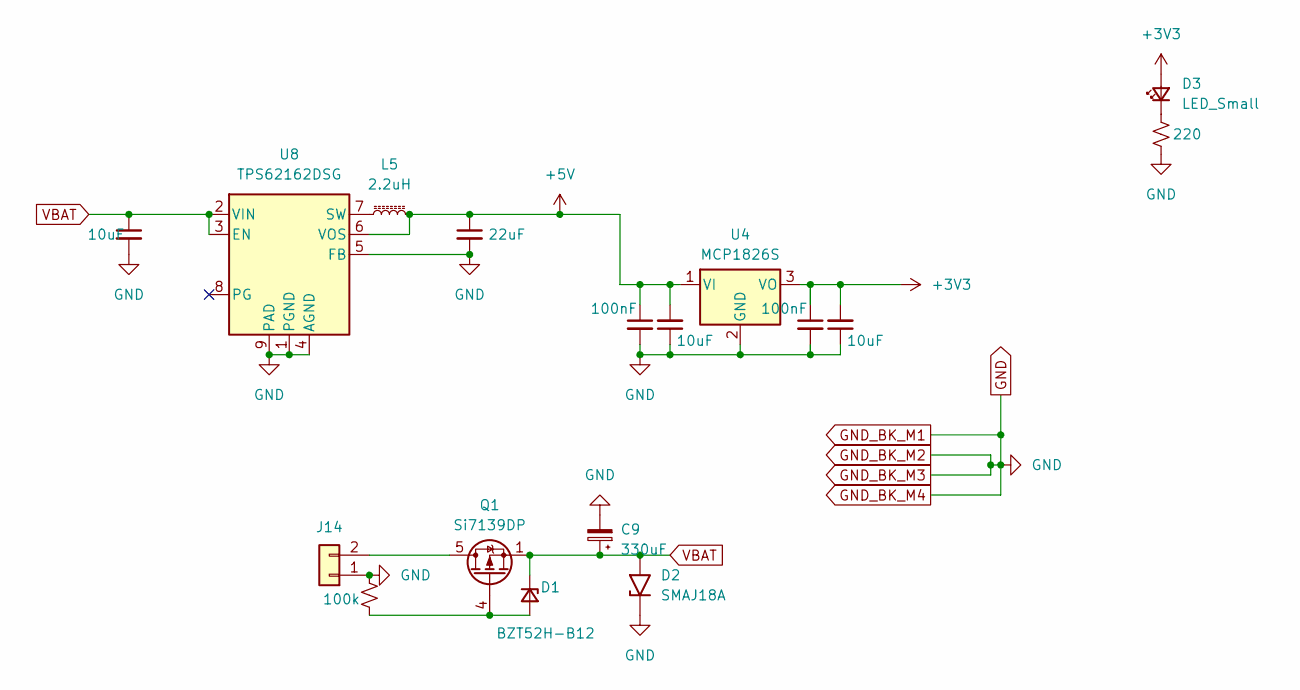
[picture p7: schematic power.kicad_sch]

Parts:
C9: 330uF; CP_Elec_10x10.5
C17, C19: 100nF; C_0603_1608Metric_Pad1.08x0.95mm_HandSolder
C18, C20, C42: 10uF; C_0603_1608Metric_Pad1.08x0.95mm_HandSolder
C43: 22uF; C_1206_3216Metric_Pad1.33x1.80mm_HandSolder
D1: BZT52H-B12; D_SOD-123
D2: SMAJ18A; D_SMA_Handsoldering
D3: LED_Small; LED_0402_1005Metric_Pad0.77x0.64mm_HandSolder
J14: Conn_01x02; SolderWire-2sqmm_1x02_P7.8mm_D2mm_OD3.9mm
L5: 2.2uH; L_1008_2520Metric_Pad1.43x2.20mm_HandSolder
Q1: Si7139DP; PowerPAK_SO-8_Single
R6: 220; R_0402_1005Metric_Pad0.72x0.64mm_HandSolder
R17: 100k; R_0402_1005Metric_Pad0.72x0.64mm_HandSolder
U4: MCP1826S; SOT-223-3_TabPin2
U8: TPS62162DSG; WSON-8-1EP_2x2mm_P0.5mm_EP0.9x1.6mm

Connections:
+3V3: C19.1, C20.2, D3.2 (A), U4.3 (VO); also elsewhere on the board
+5V: C17.1, C18.2, C43.1, L5.2, U4.1 (VI), U8.6 (VOS); also elsewhere on the board
GND: C9.2, C17.2, C18.1, C19.2, C20.1, C42.2, C43.2, D2.1 (A1), J14.1, R6.2, R17.2, U4.2 (GND), U8.1 (PGND), U8.4 (AGND), U8.5 (FB), U8.9 (PAD); also elsewhere on the board
unnamed: D1.2 (A), Q1.4 (G), R17.1
unnamed: D3.1 (K), R6.1
unnamed: J14.2, Q1.5 (D)
unnamed: L5.1, U8.7 (SW)
VBAT: C9.1, C42.1, D1.1 (K), D2.2 (A2), Q1.1 (S), Q1.2 (S), Q1.3 (S), U8.2 (VIN), U8.3 (EN); also elsewhere on the board

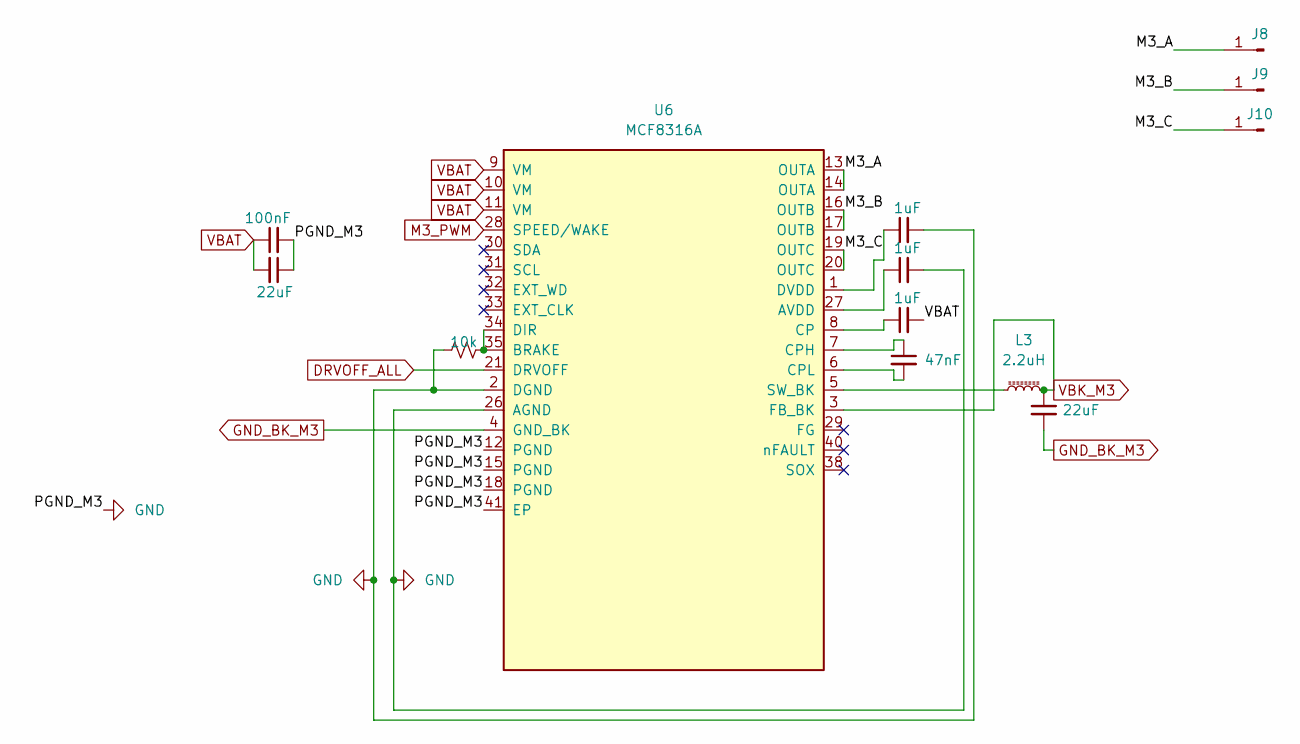
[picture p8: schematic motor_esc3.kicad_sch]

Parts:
C28: 100nF; C_0603_1608Metric_Pad1.08x0.95mm_HandSolder
C29, C34: 22uF; C_1206_3216Metric_Pad1.33x1.80mm_HandSolder
C30, C31, C32: 1uF; C_0603_1608Metric_Pad1.08x0.95mm_HandSolder
C33: 47nF; C_0603_1608Metric_Pad1.08x0.95mm_HandSolder
J8, J9, J10: SolderWirePad_1x01_SMD_2x4mm
L3: 2.2uH; L_1008_2520Metric_Pad1.43x2.20mm_HandSolder
R12: 10k; R_0402_1005Metric_Pad0.72x0.64mm_HandSolder
U6: MCF8316A; MCF8316A_RGF0040E_VQFN-40-1EP_7x5mm_P0.5mm_EP5.5x3.5mm

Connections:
/motor_esc3/M3_A: J8.1, U6.13 (OUTA), U6.14 (OUTA)
/motor_esc3/M3_B: J9.1, U6.16 (OUTB), U6.17 (OUTB)
/motor_esc3/M3_C: J10.1, U6.19 (OUTC), U6.20 (OUTC)
DRVOFF_ALL: U6.21 (DRVOFF); also elsewhere on the board
GND: C28.2, C29.1, C30.2, C31.2, C34.2, R12.1, U6.2 (DGND), U6.4 (GND_BK), U6.12 (PGND), U6.15 (PGND), U6.18 (PGND), U6.26 (AGND), U6.41 (EP); also elsewhere on the board
M3_PWM: U6.28 (SPEED/WAKE); also elsewhere on the board
unnamed: C31.1, U6.27 (AVDD)
unnamed: R12.2, U6.34 (DIR), U6.35 (BRAKE)
unnamed: C32.1, U6.8 (CP)
unnamed: C33.1, U6.7 (CPH)
unnamed: C33.2, U6.6 (CPL)
unnamed: C30.1, U6.1 (DVDD)
unnamed: L3.1, U6.5 (SW_BK)
VBAT: C28.1, C29.2, C32.2, U6.9 (VM), U6.10 (VM), U6.11 (VM); also elsewhere on the board
VBK_M3: C34.1, L3.2, U6.3 (FB_BK)

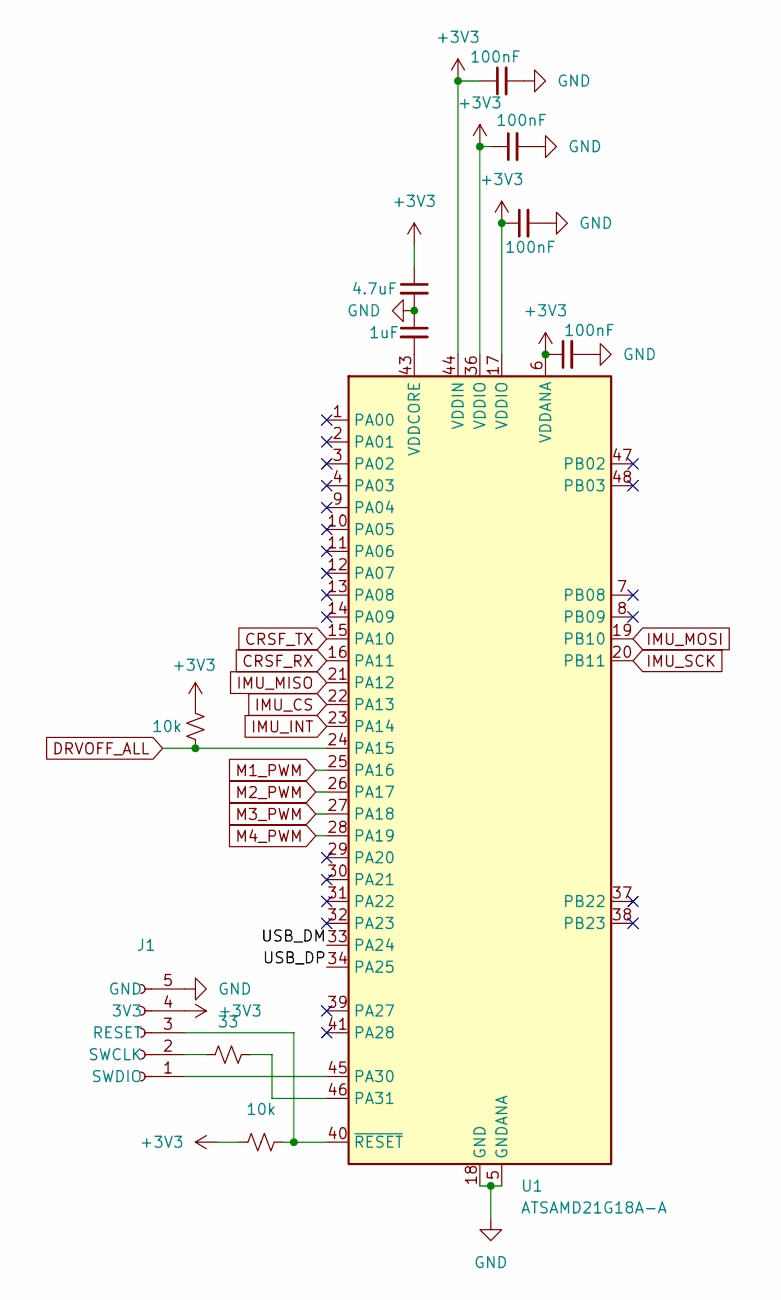
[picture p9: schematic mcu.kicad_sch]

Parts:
C1: 1uF; C_0603_1608Metric_Pad1.08x0.95mm_HandSolder
C2, C3, C4, C5: 100nF; C_0603_1608Metric_Pad1.08x0.95mm_HandSolder
C6: 4.7uF; C_0603_1608Metric_Pad1.08x0.95mm_HandSolder
J1: Conn_01x05_Socket; PinSocket_1x05_P1.00mm_Vertical_SMD_Pin1Left
R1, R4: 10k; R_0402_1005Metric_Pad0.72x0.64mm_HandSolder
R2: 33; R_0402_1005Metric_Pad0.72x0.64mm_HandSolder
U1: ATSAMD21G18A-A; TQFP-48_7x7mm_P0.5mm

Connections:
+3V3: C2.1, C3.1, C4.1, C5.1, C6.1, J1.4 (3V3), R1.1, R4.2, U1.6 (VDDANA), U1.17 (VDDIO), U1.36 (VDDIO), U1.44 (VDDIN); also elsewhere on the board
/mcu/USB_DM: U1.33 (PA24)
/mcu/USB_DP: U1.34 (PA25)
CRSF_RX: U1.16 (PA11); also elsewhere on the board
CRSF_TX: U1.15 (PA10); also elsewhere on the board
DRVOFF_ALL: R4.1, U1.24 (PA15); also elsewhere on the board
GND: C1.1, C2.2, C3.2, C4.2, C5.2, C6.2, J1.5 (GND), U1.5 (GNDANA), U1.18 (GND), U1.35 (GND), U1.42 (GND); also elsewhere on the board
IMU_CS: U1.22 (PA13); also elsewhere on the board
IMU_INT: U1.23 (PA14); also elsewhere on the board
IMU_MISO: U1.21 (PA12); also elsewhere on the board
IMU_MOSI: U1.19 (PB10); also elsewhere on the board
IMU_SCK: U1.20 (PB11); also elsewhere on the board
M1_PWM: U1.25 (PA16); also elsewhere on the board
M2_PWM: U1.26 (PA17); also elsewhere on the board
M3_PWM: U1.27 (PA18); also elsewhere on the board
M4_PWM: U1.28 (PA19); also elsewhere on the board
unnamed: J1.3 (RESET), R1.2, U1.40 (~RESET)
unnamed: J1.2 (SWCLK), R2.1
unnamed: J1.1 (SWDIO), U1.45 (PA30)
unnamed: R2.2, U1.46 (PA31)
unnamed: C1.2, U1.43 (VDDCORE)

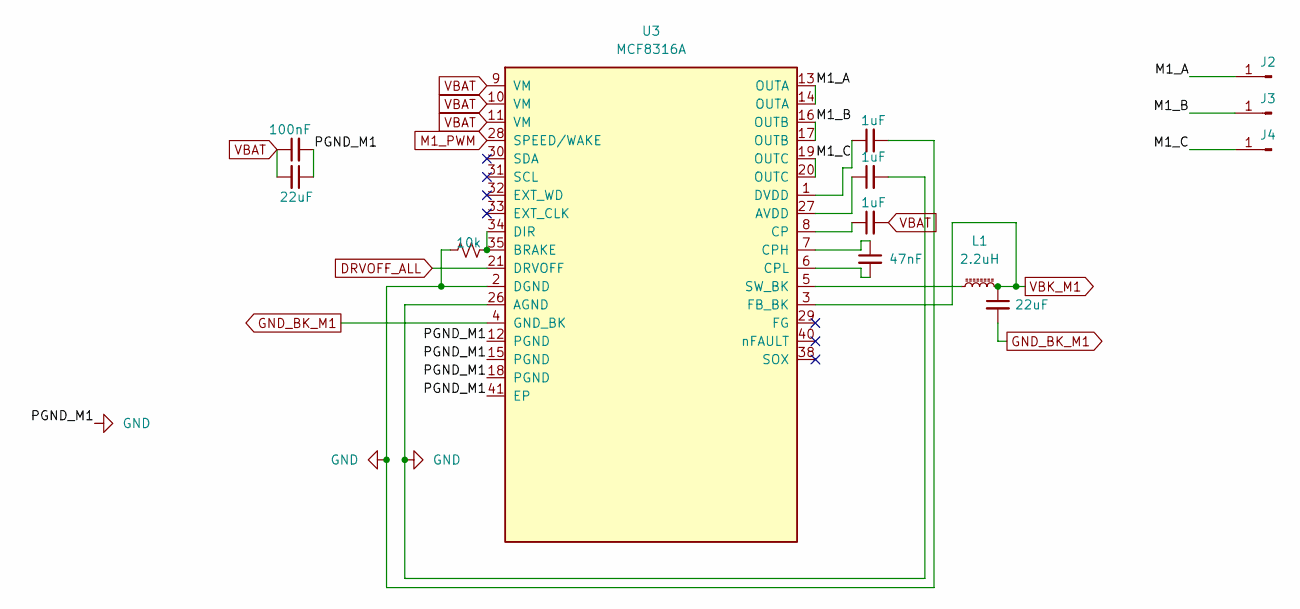
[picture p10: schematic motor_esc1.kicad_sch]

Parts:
C10, C16: 22uF; C_1206_3216Metric_Pad1.33x1.80mm_HandSolder
C11: 100nF; C_0603_1608Metric_Pad1.08x0.95mm_HandSolder
C12: 47nF; C_0603_1608Metric_Pad1.08x0.95mm_HandSolder
C13, C14, C15: 1uF; C_0603_1608Metric_Pad1.08x0.95mm_HandSolder
J2, J3, J4: SolderWirePad_1x01_SMD_2x4mm
L1: 2.2uH; L_1008_2520Metric_Pad1.43x2.20mm_HandSolder
R5: 10k; R_0402_1005Metric_Pad0.72x0.64mm_HandSolder
U3: MCF8316A; MCF8316A_RGF0040E_VQFN-40-1EP_7x5mm_P0.5mm_EP5.5x3.5mm

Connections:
/motor_esc1/M1_A: J2.1, U3.13 (OUTA), U3.14 (OUTA)
/motor_esc1/M1_B: J3.1, U3.16 (OUTB), U3.17 (OUTB)
/motor_esc1/M1_C: J4.1, U3.19 (OUTC), U3.20 (OUTC)
DRVOFF_ALL: U3.21 (DRVOFF); also elsewhere on the board
GND: C10.1, C11.2, C14.2, C15.2, C16.2, R5.1, U3.2 (DGND), U3.4 (GND_BK), U3.12 (PGND), U3.15 (PGND), U3.18 (PGND), U3.26 (AGND), U3.41 (EP); also elsewhere on the board
M1_PWM: U3.28 (SPEED/WAKE); also elsewhere on the board
unnamed: C14.1, U3.27 (AVDD)
unnamed: R5.2, U3.34 (DIR), U3.35 (BRAKE)
unnamed: C13.1, U3.8 (CP)
unnamed: C12.1, U3.7 (CPH)
unnamed: C12.2, U3.6 (CPL)
unnamed: C15.1, U3.1 (DVDD)
unnamed: L1.1, U3.5 (SW_BK)
VBAT: C10.2, C11.1, C13.2, U3.9 (VM), U3.10 (VM), U3.11 (VM); also elsewhere on the board
VBK_M1: C16.1, L1.2, U3.3 (FB_BK)

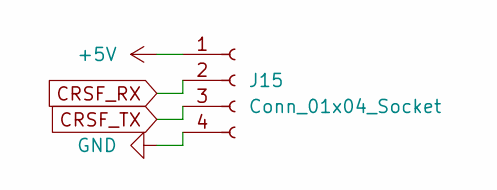
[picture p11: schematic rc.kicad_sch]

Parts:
J15: Conn_01x04_Socket; PinSocket_1x04_P1.00mm_Vertical_SMD_Pin1Left

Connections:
+5V: J15.1; also elsewhere on the board
CRSF_RX: J15.2; also elsewhere on the board
CRSF_TX: J15.3; also elsewhere on the board
GND: J15.4; also elsewhere on the board

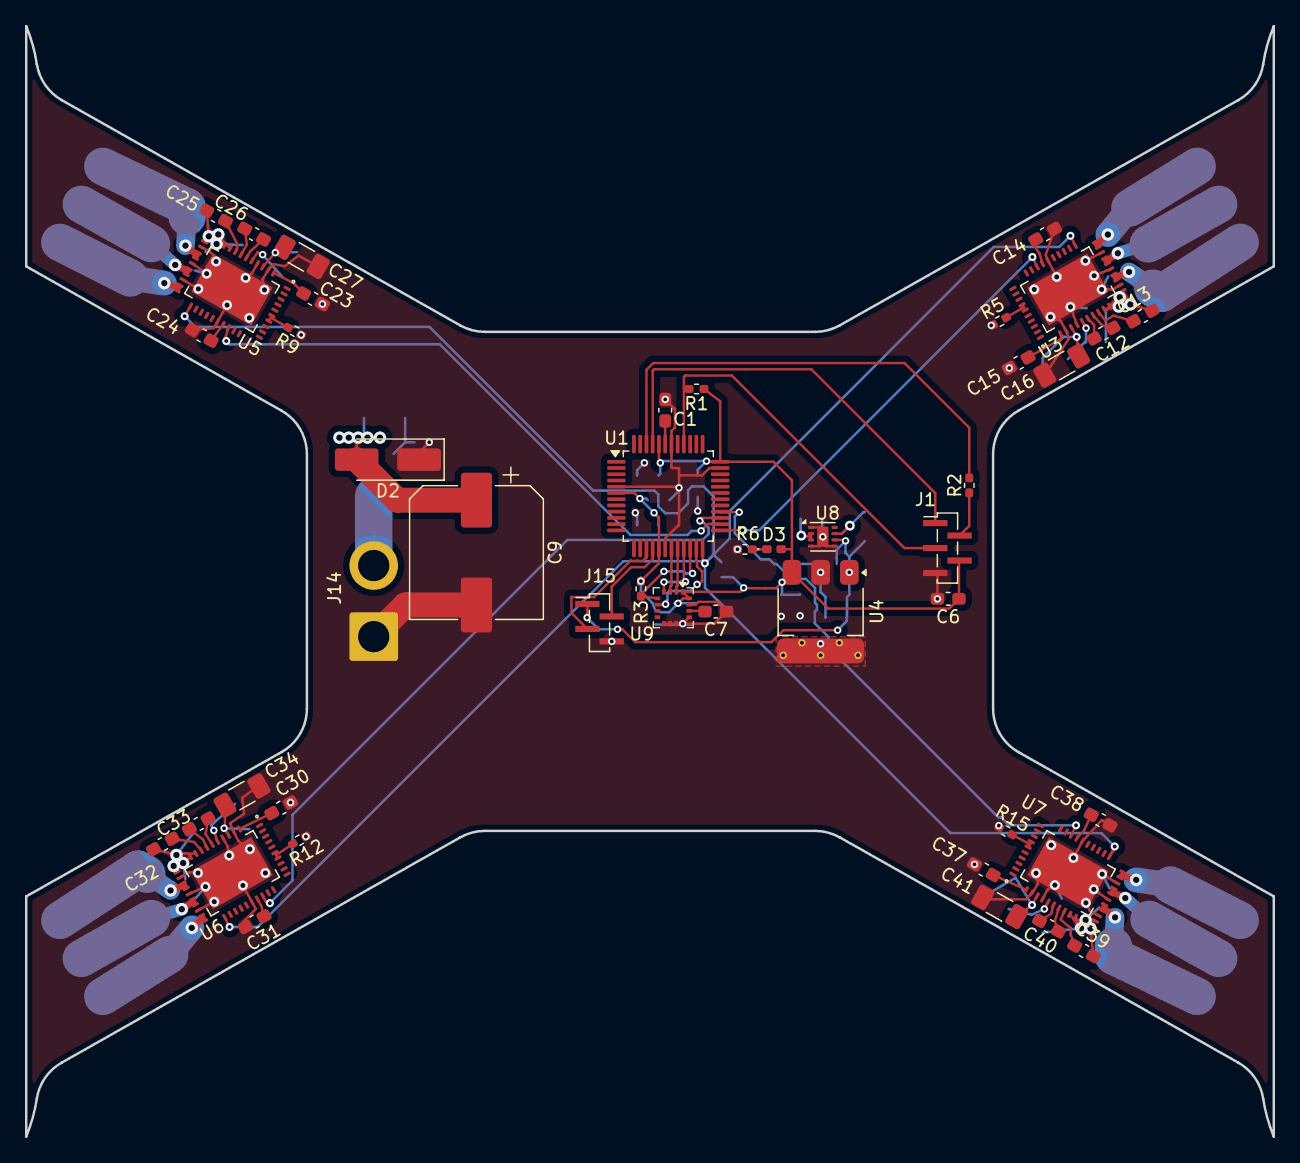
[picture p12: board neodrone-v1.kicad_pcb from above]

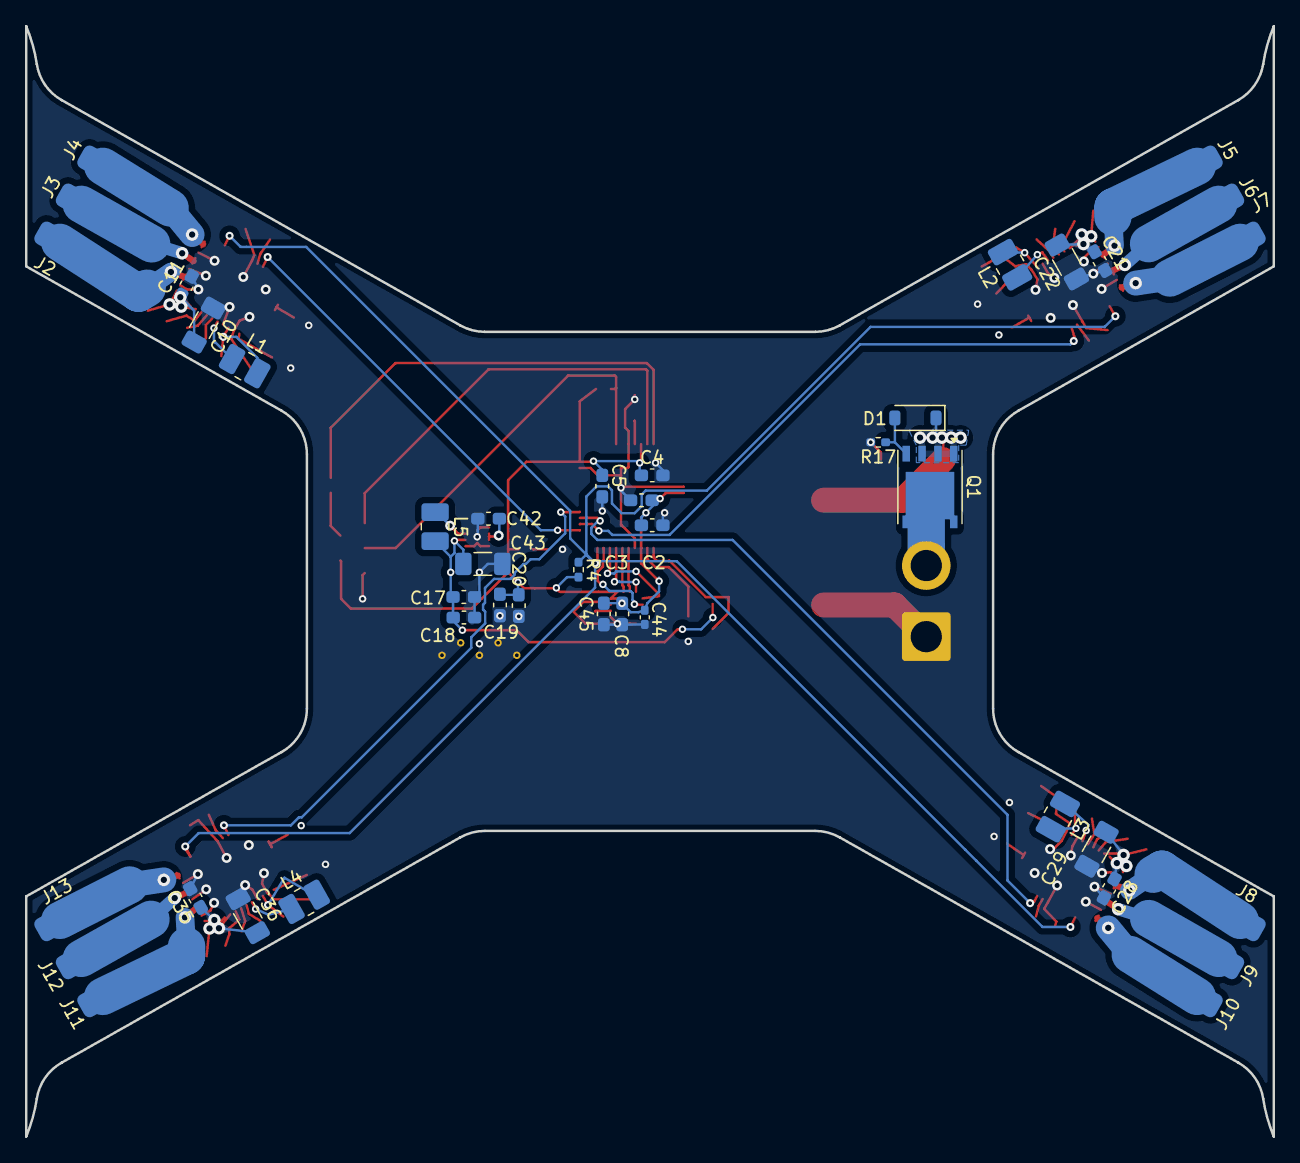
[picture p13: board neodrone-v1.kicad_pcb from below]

Board: 4 copper layers, 100.0 x 89.0 mm, 87 parts (42 on the bottom side), 70 nets.

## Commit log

2025-12-28 push files
    [imu.kicad_sch, mcu.kicad_sch, motor_esc.kicad_sch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]
2025-12-29 imu, motor esc schematics
    [imu.kicad_sch, mcu.kicad_sch, motor_esc.kicad_sch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]
2025-12-29 more esc schematics, refactoring, root schematic edits
    [imu.kicad_sch, mcu.kicad_sch, motor_esc.kicad_sch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]
2025-12-29 Schematics mostly done, netclasses, coords for esc (angled)
    [mcu.kicad_sch, motor_esc1.kicad_sch, motor_esc2.kicad_sch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]
2026-01-08 A LOT of changes, current state is 2 of 4 ESCs routed, power revamped. \n Board almost done
    [mcu.kicad_sch, motor_esc1.kicad_sch, motor_esc2.kicad_sch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]
2026-01-08 A LOT of changes, current state is 2 of 4 ESCs routed, power revamped. #2 \n Board almost done
    [freerouting.dsn]
2026-01-16 done #2
    [bom.csv, designators.csv, positions.csv]
2026-02-09 Remove obsolete files: deleted positions.csv, and lock files for PCB and schematic
    [bom-digikey.csv, bom.csv, designators.csv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]
